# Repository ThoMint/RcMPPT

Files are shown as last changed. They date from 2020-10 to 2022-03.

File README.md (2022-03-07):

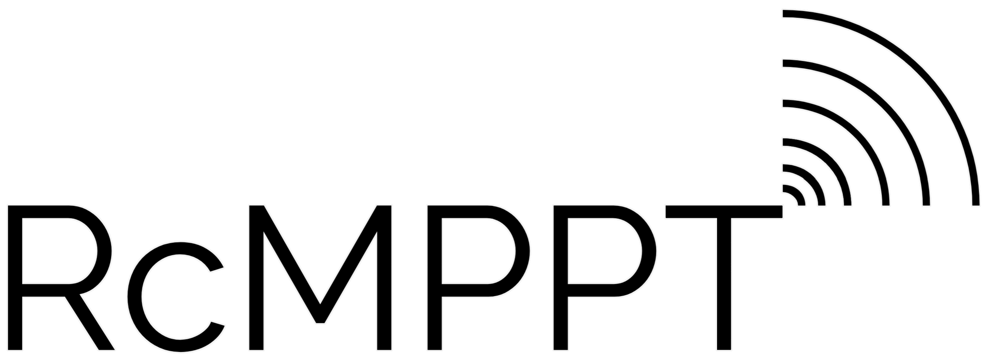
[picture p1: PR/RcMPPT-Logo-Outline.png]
RcMPPT

An MPPT Solar Charge Controller geared towards solar-powered RC model aircrafts and rovers\
\
Features:\
-SBUS/SPI/CAN/I2C/UART/USB Interface\
-Maximum Power Point Tracking\
-Extremely space/cost efficient\
-Ultra wide Vin/Vout Range 0-100V\
-High current capability 20A\

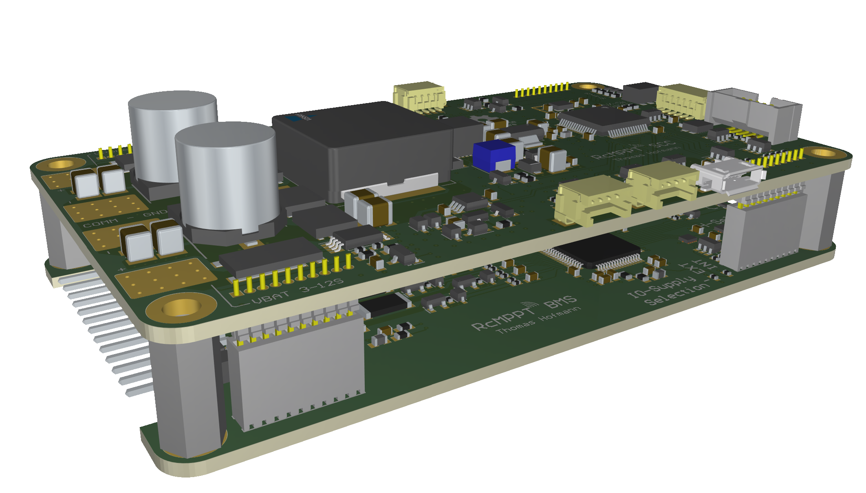
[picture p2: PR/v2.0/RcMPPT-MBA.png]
Side View of MBA Prototype


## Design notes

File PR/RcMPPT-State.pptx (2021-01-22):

## Rc-MPPT

Der Solar Charge Controller für Modellbau

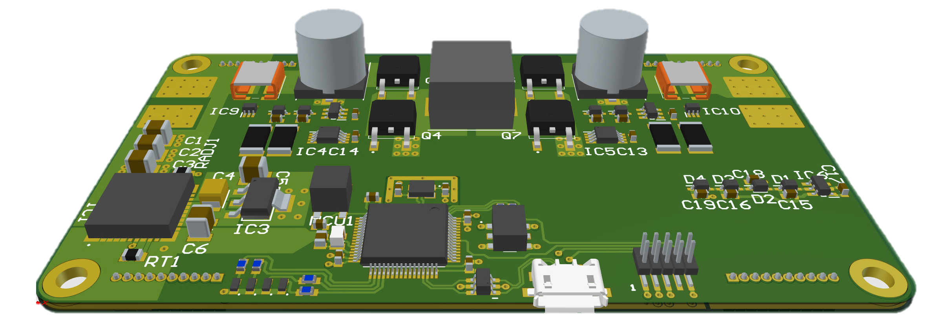
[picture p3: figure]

## Ziele: Project-Rover

- Solarbetriebenes Fahrzeug
- Testplattform für eigene Hardware
- Autonom (GPS-Wegpunktmissionen)

Hofmann Thomas 4BHELS

## Umfang: Project-Rover

- Solar-Rover als Testplattform für:
  - RcMPPT – Solarladeregler: modular | platz- und kosteneffizient | MPPT | Cell Balancing | 3-12S | Open Source
  - ModFOC – Motorregler: modular | platz-, kosten- und energieeffizient | BLDC / Stepper / DC | 3-12S | Open Source
  - Flexible Solarzellen: mögliche weitere Anwendungen evaluieren (Project-Airplane?)

## Motivation

- Technische Herausforderung
- Noch keine derartige Hardware für Modellbau auf dem Markt / Open Source

## Aufbau: RcMPPT

- MCU-getakteter 4-SW Buck Boost
  - Technische Herausforderung
  - Volle Kontrolle über Regelverhalten (CC, CV, Softstart, etc.) durch HRTIM
  - Kostenersparnis
- Logic Supply: 5V Rail Integrated Inductor Buck Schaltwandler
  - Kostenersparnis
  - Platzersparnis
- STM32G474RE
  - 32Bit MCU
  - Interfaces: S-BUS, I2C, SPI, CAN, USB, etc.

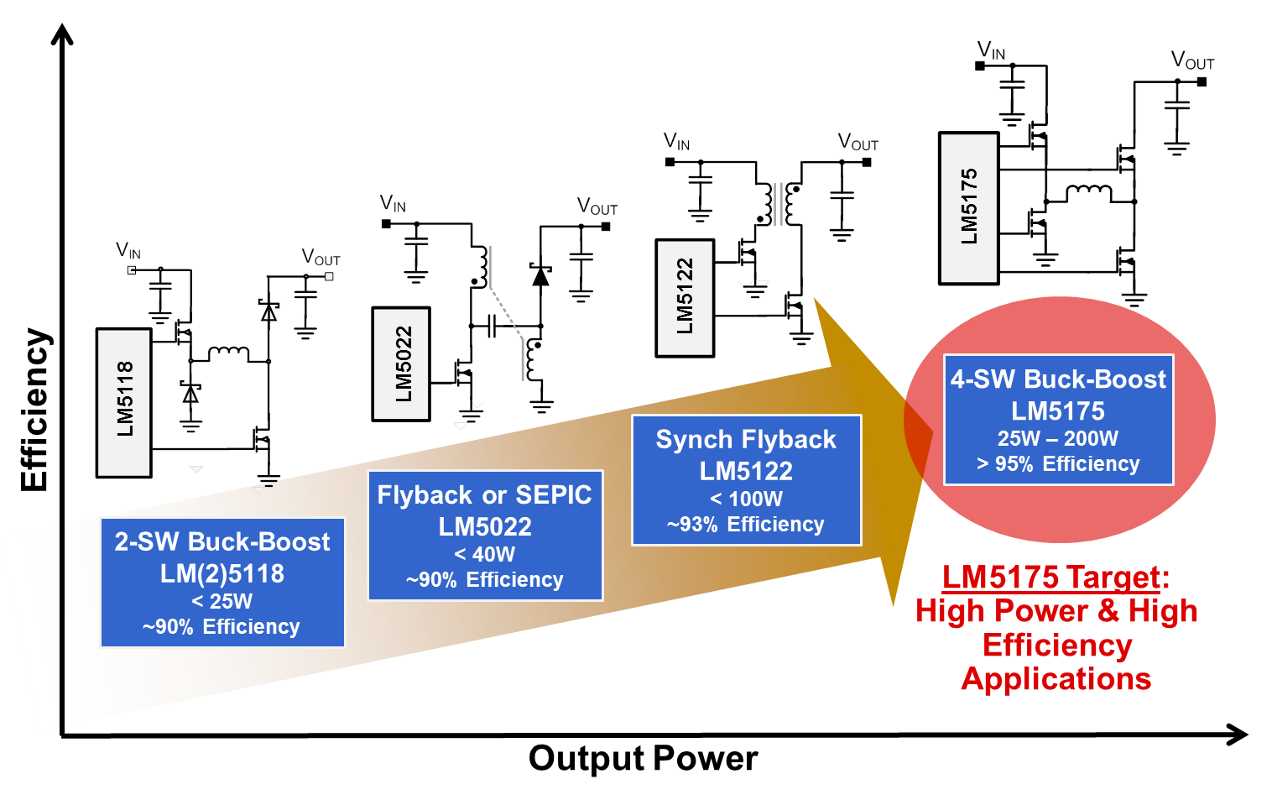
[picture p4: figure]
Four-switch buck-boost controller delivers high power and efficiency - Power management - Technical articles - TI E2E support forums

## Maximum Power Point Tracking

- Tracking durch Software
- Energiepuffer wird benötigt

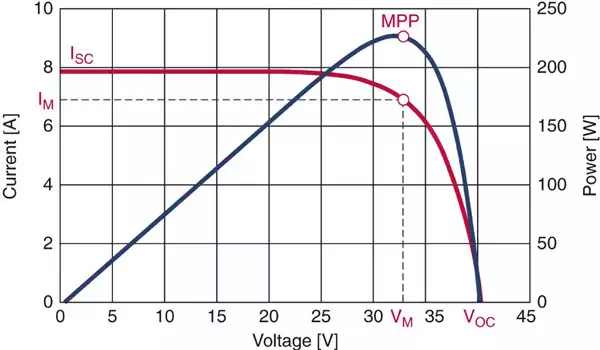
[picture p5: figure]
Maximum Power Point Tracking | BLUEsat UNSW

## Herausforderungen: RcMPPT

- Große Input / Output Voltage Range
  - 3-12S Output Voltage (6-60V)
  - 5V Logic Rail muss durch Buck Converter generiert werden (muss mit hohem Duty-Cycle arbeiten können)
- 4-Switch Buck Boost
  - High Side N-Kanal Mosfets -> Bootstrap Treiber
  - Für optimale Effizienz: Duty Cycle von 100% notwendig -> Floating Charge Pump
  - Hohe Schaltfrequenz

## Schematik: RcMPPT - MCU

- MCU
  - STM32G474RB
- Peripherie
  - Signal LEDS
  - Crystal Oszillator
  - USB
  - Decoupling / Analog Supply Filtering

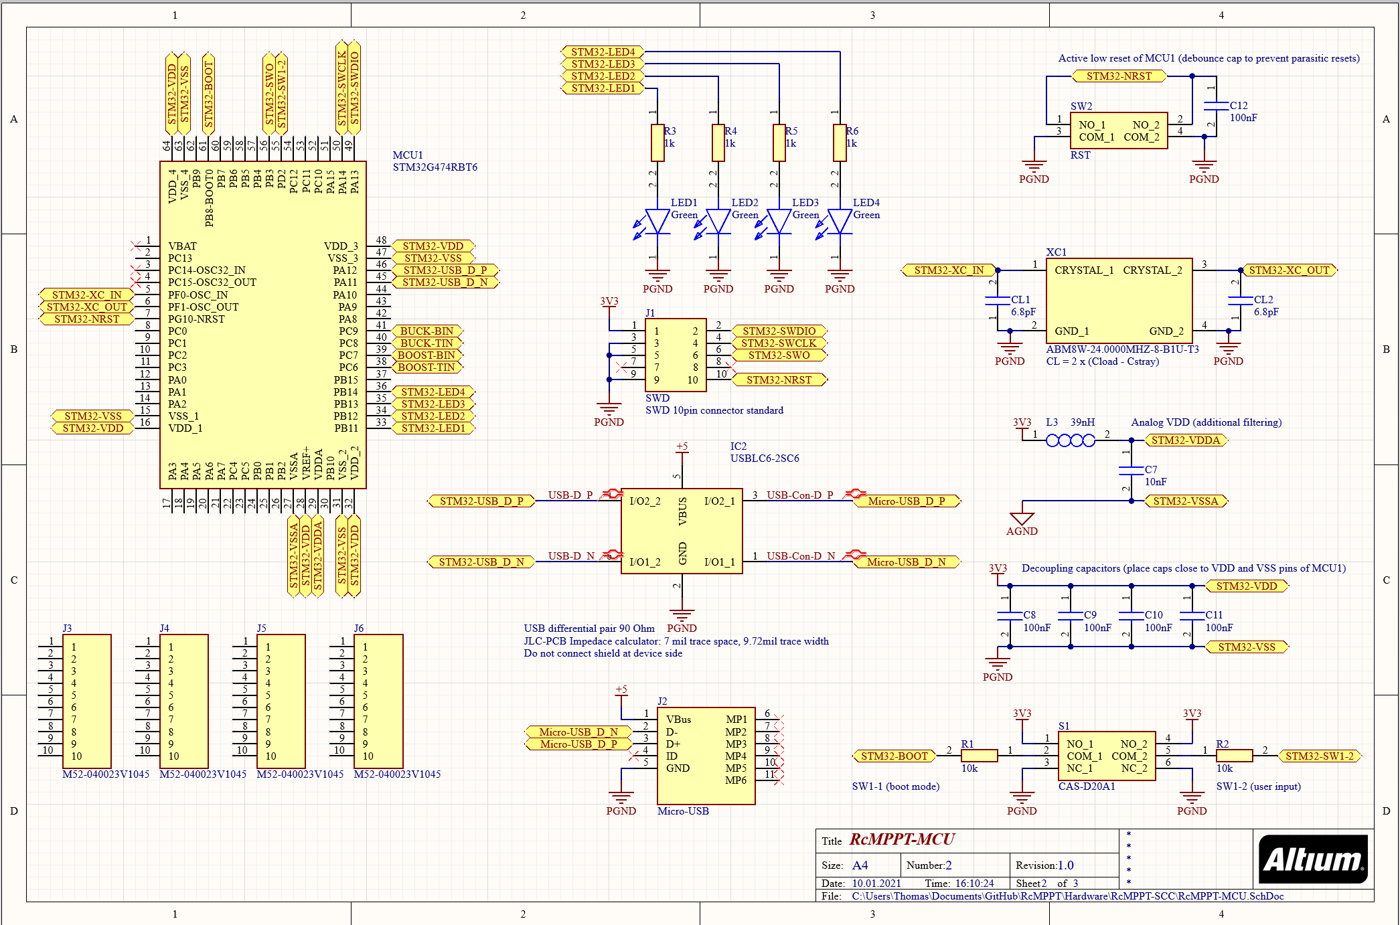
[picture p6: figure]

## SchematiK: RcMPPT – Power Module

- LMZ3600
  - Integrated Inductor
  - AGND, PGND
- 3V3 LDO
  - Low Ripple
  - Precision

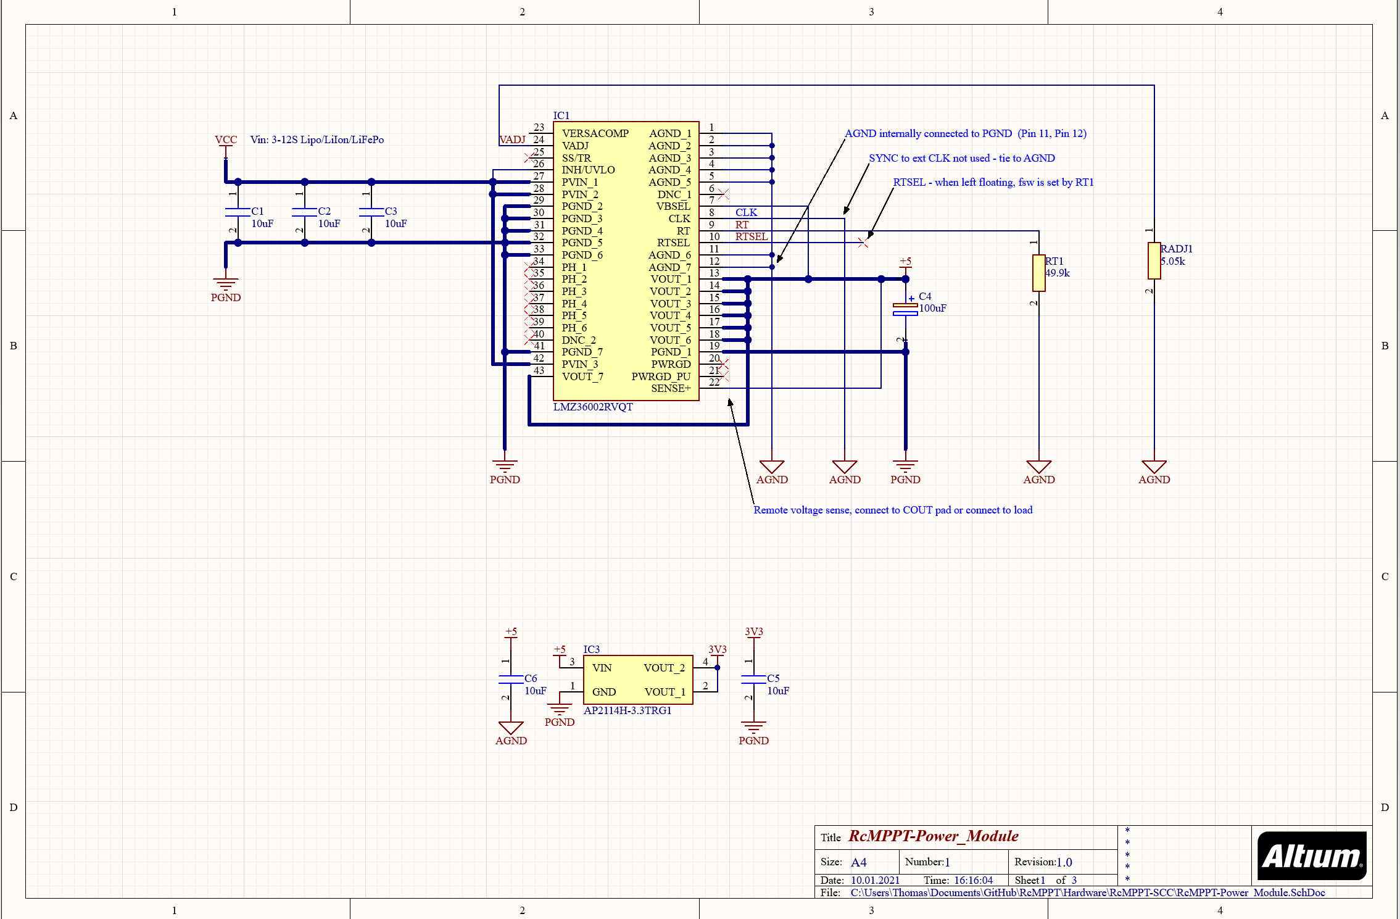
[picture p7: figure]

## Schematik: RcMPPT - DCDC

- 4Sw Buck Boost
  - Bootstrap Gate Driver
  - Floating Charge Pump (100% Duty Cycle)

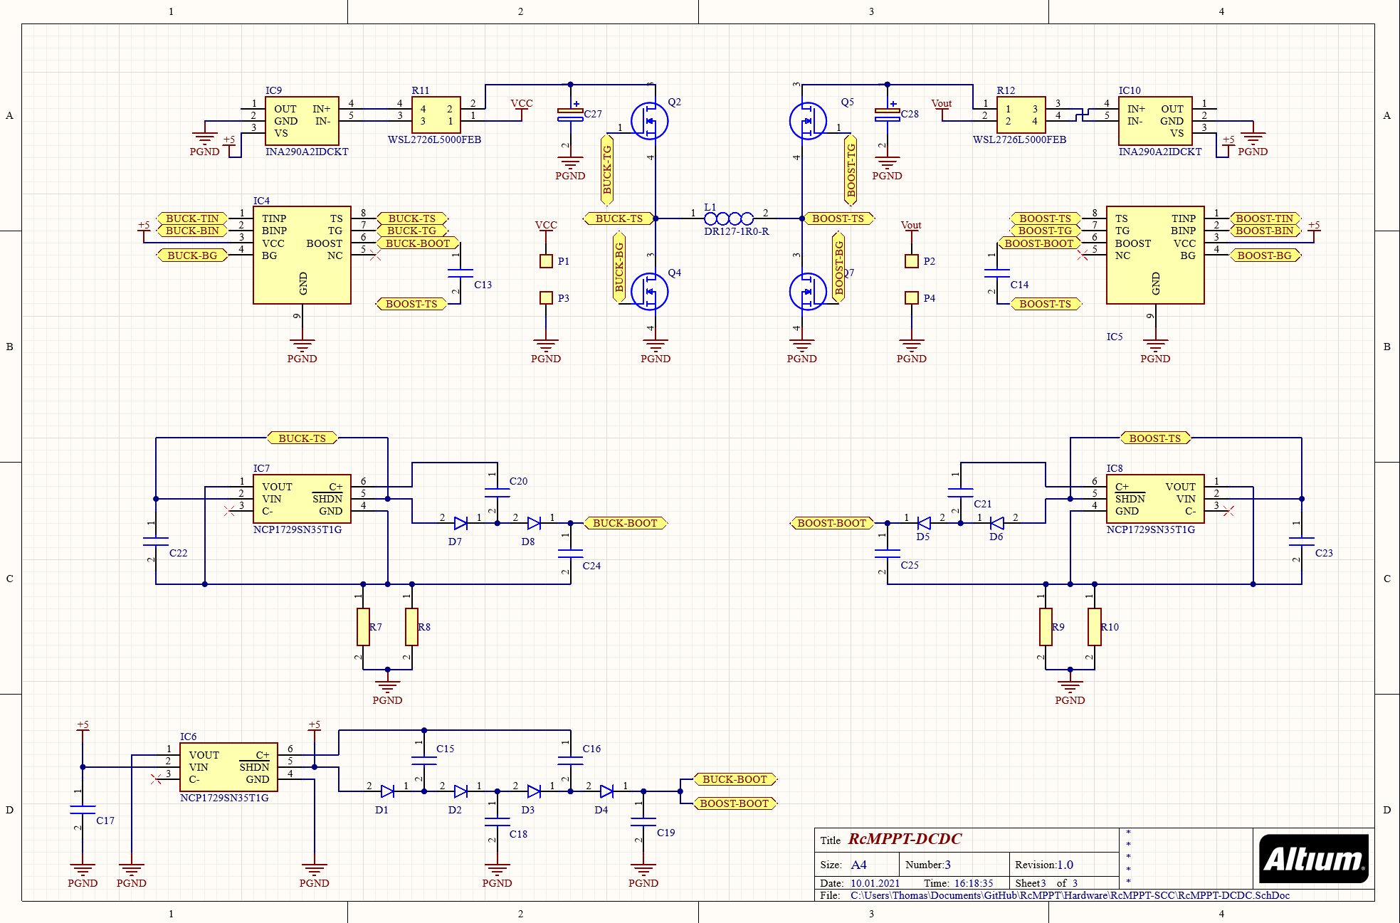
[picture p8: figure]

## Softwareentwicklung

- STM32CubeIDE
  - GUI Konfiguration von
    - Timer
    - Clock
    - Interfaces

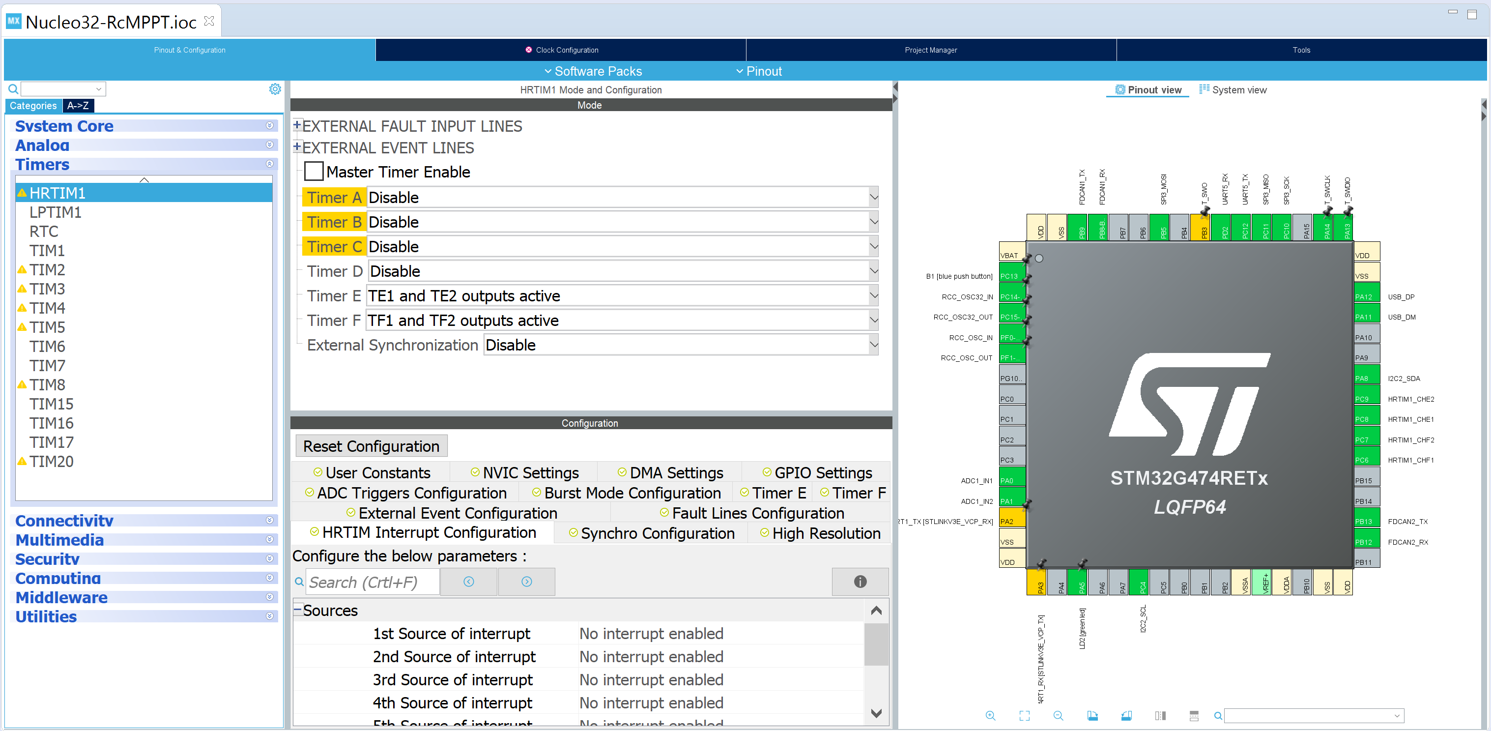
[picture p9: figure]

## Weitere Entwicklung

- PCB-Stackup
  - Solar Charge Controller
  - Battery Management System
- Software entwicklung
  - RcMPPT
  - ModFOC

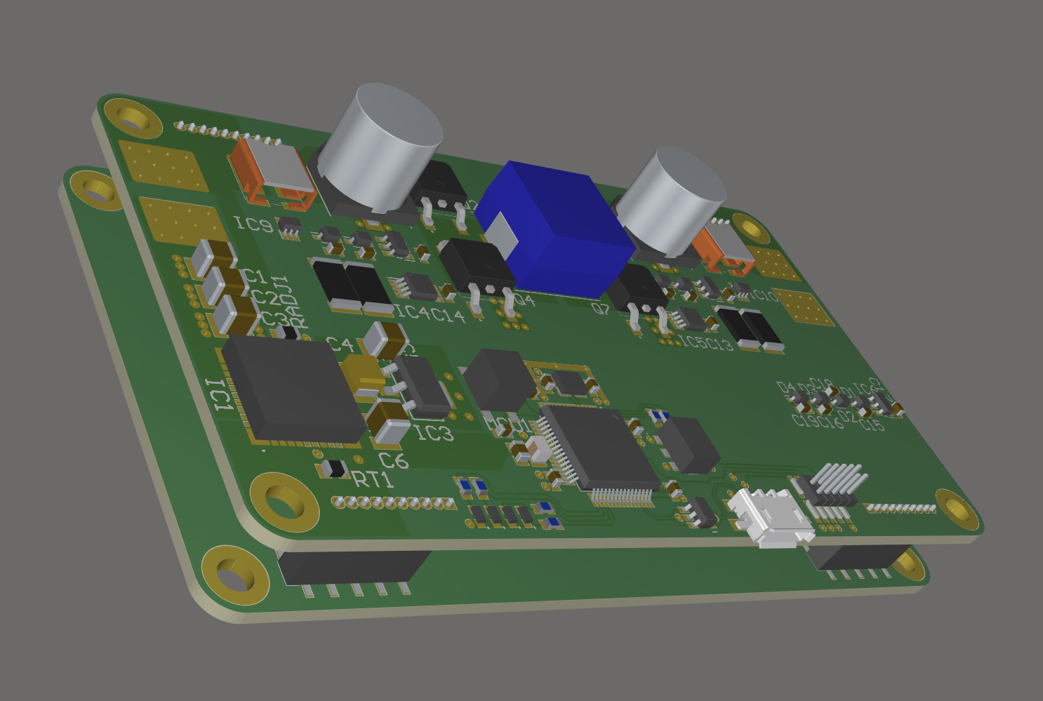
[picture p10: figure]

## Ende

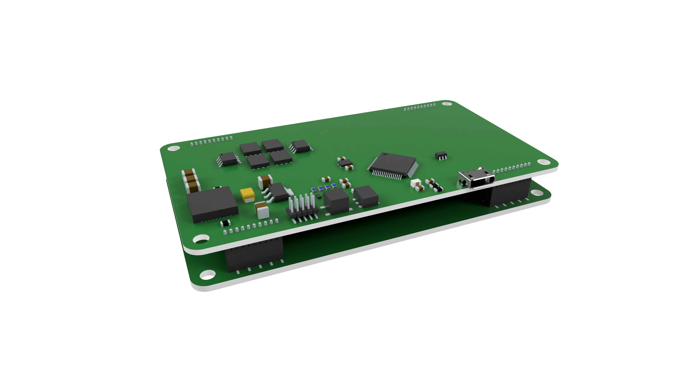
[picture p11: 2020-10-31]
Hardware/v2.0/RcMPPT/First_MBA_Prototype.png

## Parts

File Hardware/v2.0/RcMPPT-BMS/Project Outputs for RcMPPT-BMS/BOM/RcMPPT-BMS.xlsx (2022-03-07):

Comment | Description | Designator | Footprint | LibRef | Manufacturer_Part_Number | Manufacturer_Name | Mouser Part Number | Quantity
22-28-8133 | Connector | J1 | HDRRA13W66P0X254_1X13_3302X229X249P | 22-28-8133 | 22-28-8133 | Molex | 538-22-28-8133 | 1
BQ76PL536APAPT | Integrated Circuit | IC100, IC200 | QFP50P1200X1200X120-65N | BQ76PL536APAPT | BQ76PL536APAPT | Texas Instruments | 595-BQ76PL536APAPT | 2
2.2uF 10V | Capacitor | C108, C109, C110, C112, C114, C209, C210, C212, C214, C215 | CAPC1608X97N | C0603 | CL10A225KO8NNNC | Samsung Electro-Mechanics | 187-CL10A225KO8NNNC | 10
47nF 16V | Capacitor | C115, C116, C203, C204 | CAPC1608X97N | C0603 | CL10B473KO8NNNC | Samsung Electro-Mechanics | 187-CL10B473KO8NNNC | 4
100nF 6.3V | Capacitor | C400, C401 | CAPC1608X97N | C0603 | C0603C104K9RACTU | KEMET | 80-C0603C104K9R | 2
100nF 50V | Capacitor | C1, C100, C101, C102, C103, C104, C105, C106, C107, C111, C113, C200, C201, C202, C205, C206, C207, C208, C211, C213, C216, C300_U_RcMPPT-BMS-BFE-1-1, C300_U_RcMPPT-BMS-BFE-1-2, C300_U_RcMPPT-BMS-BFE-1-3, C300_U_RcMPPT-BMS-BFE-1-4, C300_U_RcMPPT-BMS-BFE-1-5, C300_U_RcMPPT-BMS-BFE-1-6, C300_U_RcMPPT-BMS-BFE-2-1, C300_U_RcMPPT-BMS-BFE-2-2, C300_U_RcMPPT-BMS-BFE-2-3, C300_U_RcMPPT-BMS-BFE-2-4, C300_U_RcMPPT-BMS-BFE-2-5, C300_U_RcMPPT-BMS-BFE-2-6 | CAPC1608X97N | C0603 | CL10B104JB8NNNC | Samsung Electro-Mechanics | 187-CL10B104JB8NNNC | 33
Green | LED | LED100, LED200 | CHIPLED_0603 | CHIPLED0603 | LT Q39G-Q1OO-25-1 | ams OSRAM | 720-LTQ39GQ1S22515 | 2
10k 1% NTC | Thermistor | RT100, RT101, RT200, RT201 | THRMC1608X90N | ERT-J1VG103FA | ERT-J1VG103FA | Panasonic | 667-ERT-J1VG103FA | 4
ESDSUPPRESSOR | TVS Diode Array | D400, D401 | SOT23-6 | ESDSUPPRESSOR | ESDALD05UD4X | WeEn Semiconductors | 771-ESDALD05UD4X | 2
60V 2A | MOSFET (N-Channel) | Q100, Q200, Q300_U_RcMPPT-BMS-BFE-1-1, Q300_U_RcMPPT-BMS-BFE-1-2, Q300_U_RcMPPT-BMS-BFE-1-3, Q300_U_RcMPPT-BMS-BFE-1-4, Q300_U_RcMPPT-BMS-BFE-1-5, Q300_U_RcMPPT-BMS-BFE-1-6, Q300_U_RcMPPT-BMS-BFE-2-1, Q300_U_RcMPPT-BMS-BFE-2-2, Q300_U_RcMPPT-BMS-BFE-2-3, Q300_U_RcMPPT-BMS-BFE-2-4, Q300_U_RcMPPT-BMS-BFE-2-5, Q300_U_RcMPPT-BMS-BFE-2-6 | SOT96P240X110-3N | NMOS | PMV37ENEAR | Nexperia | 771-PMV37ENEAR | 14
0R | Resistor | R114, R203, R408, R409 | RESC1005X40N | R0402 | ERJ-2GE0R00X | Panasonic | 667-ERJ-2GE0R00X | 4
1k | Resistor | R1, R2, R3, R4, R5, R6, R7, R8, R100, R101, R102, R103, R104, R105, R106, R107, R108, R109, R110, R111, R112, R205, R206, R207, R208, R209, R212, R215, R216, R218, R220, R221, R222, R223 | RESC1005X40N | R0402 | CR0402-FX-1001GLF | Bourns | 652-CR0402FX-1001GLF | 34
1M | Resistor | R301_U_RcMPPT-BMS-BFE-1-1, R301_U_RcMPPT-BMS-BFE-1-2, R301_U_RcMPPT-BMS-BFE-1-3, R301_U_RcMPPT-BMS-BFE-1-4, R301_U_RcMPPT-BMS-BFE-1-5, R301_U_RcMPPT-BMS-BFE-1-6, R301_U_RcMPPT-BMS-BFE-2-1, R301_U_RcMPPT-BMS-BFE-2-2, R301_U_RcMPPT-BMS-BFE-2-3, R301_U_RcMPPT-BMS-BFE-2-4, R301_U_RcMPPT-BMS-BFE-2-5, R301_U_RcMPPT-BMS-BFE-2-6 | RESC1005X40N | R0402 | RC0402FR-071ML | YAGEO | 603-RC0402FR-071ML | 12
2k2 | Resistor | R116, R200 | RESC1005X40N | R0402 | RC0402FR-072K2L | YAGEO | 603-RC0402FR-072K2L | 2
100k | Resistor | R113, R117, R201, R202 | RESC1005X40N | R0402 | ERJ-U02F1003X | Panasonic | 667-ERJ-U02F1003X | 4
100R | Resistor | R118, R119, R120, R204, R210, R211, R400, R401, R402, R403, R404, R405, R406, R407 | RESC1005X40N | R0402 | AC0402FR-13100RL | YAGEO | 603-AC0402FR-13100RL | 14
1.47k 1% | Resistor | R121, R122, R213, R214 | RESC1608X50N | R0603 | CR0603-FX-1471ELF | Bourns | 652-CR0603FX-1471ELF | 4
1.82k 1% | Resistor | R123, R124, R217, R219 | RESC1608X50N | R0603 | CR0603-FX-1821ELF | Bourns | 652-CR0603FX-1821ELF | 4
10R 1W | Resistor | R300_U_RcMPPT-BMS-BFE-1-1, R300_U_RcMPPT-BMS-BFE-1-2, R300_U_RcMPPT-BMS-BFE-1-3, R300_U_RcMPPT-BMS-BFE-1-4, R300_U_RcMPPT-BMS-BFE-1-5, R300_U_RcMPPT-BMS-BFE-1-6, R300_U_RcMPPT-BMS-BFE-2-1, R300_U_RcMPPT-BMS-BFE-2-2, R300_U_RcMPPT-BMS-BFE-2-3, R300_U_RcMPPT-BMS-BFE-2-4, R300_U_RcMPPT-BMS-BFE-2-5, R300_U_RcMPPT-BMS-BFE-2-6 | RESC6331X75N | R2512 | CR2512-JW-100ELF | Bourns | 652-CR2512-JW-100ELF | 12
SMS-110-01-G-S | 10 Position Receptacle Connector 0.050" (1.27mm) Through Hole Gold | J400, J401, J402, J403 | SAMTEC_SMS-110-X-X-S | SMS-110-X-X-S | SMS-110-01-G-S | Samtec | 200-SMS11001GS | 4
TXU0304RUTR | Integrated Circuit | IC400, IC401 | UQFN-12 | TXU0304RUTR | TXU0304RUTR | Texas Instruments | 595-TXU0304RUTR | 2
5.1V 200mW | ZENER Diode | D301_U_RcMPPT-BMS-BFE-1-1, D301_U_RcMPPT-BMS-BFE-1-2, D301_U_RcMPPT-BMS-BFE-1-3, D301_U_RcMPPT-BMS-BFE-1-4, D301_U_RcMPPT-BMS-BFE-1-5, D301_U_RcMPPT-BMS-BFE-1-6, D301_U_RcMPPT-BMS-BFE-2-1, D301_U_RcMPPT-BMS-BFE-2-2, D301_U_RcMPPT-BMS-BFE-2-3, D301_U_RcMPPT-BMS-BFE-2-4, D301_U_RcMPPT-BMS-BFE-2-5, D301_U_RcMPPT-BMS-BFE-2-6 | SOD-323 | ZENER-DIODE | MMXZ5231B-TP | Micro Commercial Components (MCC) | 833-MMXZ5231B-TP | 12
5.6V 400mW | ZENER Diode | D300_U_RcMPPT-BMS-BFE-1-1, D300_U_RcMPPT-BMS-BFE-1-2, D300_U_RcMPPT-BMS-BFE-1-3, D300_U_RcMPPT-BMS-BFE-1-4, D300_U_RcMPPT-BMS-BFE-1-5, D300_U_RcMPPT-BMS-BFE-1-6, D300_U_RcMPPT-BMS-BFE-2-1, D300_U_RcMPPT-BMS-BFE-2-2, D300_U_RcMPPT-BMS-BFE-2-3, D300_U_RcMPPT-BMS-BFE-2-4, D300_U_RcMPPT-BMS-BFE-2-5, D300_U_RcMPPT-BMS-BFE-2-6 | SOD-123FL | ZENER-DIODE | NZH5V6B,115 | Nexperia | 771-NZH5V6B-115 | 12

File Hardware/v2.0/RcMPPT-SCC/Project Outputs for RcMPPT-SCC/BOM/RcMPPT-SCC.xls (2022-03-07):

Designator | Comment | DesignItemId | Footprint | Manufacturer_Part_Number | Manufacturer_Name | Mouser Part Number | Quantity
R106, R107, R410, R411, R504, R505, R506, R507 | 1k | R0603 | RESC1608X50N | CR0603-FX-1001ELF (https://www.mouser.at/ProductDetail/Bourns/CR0603-FX-1001ELF) | Bourns (https://www.mouser.at/manufacturer/bourns/) | 652-CR0603FX-1001ELF | 8
R414, R601 | 1M | R0603 | RESC1608X50N | RC0603FR-131ML (https://www.mouser.at/ProductDetail/YAGEO/RC0603FR-131ML?qs=sGAEpiMZZMvdGkrng054t8AJgcdMkx7xUtJ5VXpD6XA%3D) | YAGEO (https://www.mouser.at/manufacturer/yageo/) | 603-RC0603FR-131ML | 2
R104, R105, R310, R311 | 2k | R0603 | RESC1608X50N | RK73B1JTTD202J (https://www.mouser.at/ProductDetail/KOA-Speer/RK73B1JTTD202J) | KOA Speer (https://www.mouser.at/manufacturer/koa-speer/) | 660-RK73B1JTTD202J | 4
R304, R305 | 2k | R0402 | RESC1005X40N | ERJ-2RKF2001X (https://www.mouser.at/ProductDetail/Panasonic/ERJ-2RKF2001X?qs=sGAEpiMZZMvdGkrng054t8ugkoYZivkgNOCNyJBEp2c%3D) | Panasonic (https://www.mouser.at/manufacturer/panasonicec/) | 667-ERJ-2RKF2001X | 2
IC600 | 3V3 >800mA | LDO-SOT223 | SOT230P700X180-4N | NCP1117ST33T3G (https://www.mouser.at/ProductDetail/onsemi/NCP1117ST33T3G) | onsemi (https://www.mouser.at/manufacturer/onsemi/) | 863-NCP1117ST33T3G | 1
C306, C307, C316, C317 | 3.3uF 16V | C0603 | CAPC1608X97N | C1608X5R1C335K080AC (https://www.mouser.at/ProductDetail/TDK/C1608X5R1C335K080AC?qs=U4gclJHtfSguGhrrYC%2Fi2g%3D%3D) | TDK (https://www.mouser.at/manufacturer/tdk/) | 810-C1608X5R1C335KAC | 4
R308, R309 | 4k3 | R0603 | RESC1608X50N | CR0603-JW-432ELF (https://www.mouser.at/ProductDetail/Bourns/CR0603-JW-432ELF) | Bourns (https://www.mouser.at/manufacturer/bourns/) | 652-CR0603JW-432ELF | 2
CL100, CL101 | 4nF 6.3V | C0603 | CAPC1608X97N | CL10C040CB8NNNC (https://www.mouser.at/ProductDetail/Samsung-Electro-Mechanics/CL10C040CB8NNNC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) | Samsung (https://www.mouser.at/manufacturer/samsung-electro-mechanics/) | 187-CL10C040CB8NNNC | 2
C201, C202 | 4.7uF 100V | C1210 | CAPC3225X270N | CL32B475KCVZNWE (https://www.mouser.at/ProductDetail/Samsung-Electro-Mechanics/CL32B475KCVZNWE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) | Samsung | 187-CL32B475KCVZNWE | 2
R300, R301 | 5mR 4W | FC4L90R005FER | FC4L90R005FER | FC4L90R005FER | Ohmite | 588-FC4L90R005FER | 2
R100, R102, R103, R400, R403, R404, R409 | 10k | R0603 | RESC1608X50N | RC0603JR-0710KL (https://www.mouser.at/ProductDetail/YAGEO/RC0603JR-0710KL?qs=sGAEpiMZZMvdGkrng054txdMlaQGj9fi5a0YMwYlB2s%3D) | YAGEO (https://www.mouser.at/manufacturer/yageo/) | 603-RC0603JR-0710KL | 7
C105, C112, C401 | 10nF 6.3V | C0603 | CAPC1608X97N | C0603C103K9RACTU (https://www.mouser.at/ProductDetail/KEMET/C0603C103K9RACTU?qs=r%2FVmNO8Tjq6U7vsVOlbauA%3D%3D) | KEMET (https://www.mouser.at/manufacturer/kemet-electronics/) | 80-C0603C103K9R | 3
C600, C601 | 10uF 6.3V X7R | C1206 | CAPC3216X180N | CL31B106KQHNFNE (https://www.mouser.at/ProductDetail/Samsung-Electro-Mechanics/CL31B106KQHNFNE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) | Samsung | 187-CL31B106KQHNFNE | 2
C308, C309 | 10uF 16V | C0805 | CAPC2012X88N | CL21A106KOQNNNG (https://www.mouser.at/ProductDetail/Samsung-Electro-Mechanics/CL21A106KOQNNNG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) | Samsung | 187-CL21A106KOQNNNG | 2
C603, C604 | 10uF 25V X7R | C1210 | CAPC3225X270N | TMK325B7106KN-TR (https://www.mouser.at/ProductDetail/Taiyo-Yuden/TMK325B7106KN-TR?qs=PzICbMaShUf6mn8bIhLveg%3D%3D) | Taiyo Yuden (https://www.mouser.at/manufacturer/taiyo-yuden/) | 963-TMK325B7106KN-TR | 2
C300, C301, C302, C303, C312, C313, C314, C315 | 10uF 100V | C1210 | CAPC3225X270N | GRM32EC72A106KE05L | Murata Electronics | 81-GRM32EC72A106KE05 | 8
L600 | 12uH | 78438357100 | INDPM4141X310N | 78438357100 | Wurth Elektronik | 710-78438357100 | 1
R602 | 13.3k | R0603 | RESC1608X50N | ERJ-3EKF1332V (https://www.mouser.at/ProductDetail/Panasonic/ERJ-3EKF1332V?qs=sGAEpiMZZMvdGkrng054t8ugkoYZivkgWToiCCR9eDI%3D) | Panasonic (https://www.mouser.at/manufacturer/panasonicec/) | 667-ERJ-3EKF1332V | 1
Y100 | 16Mhz 8pF | ABM8W-16.0000MHZ-8-B1U-T3 | ABM8W160000MHZ8B1UT3 | ABM8W-16.0000MHZ-8-B1U-T3 | ABRACON | 815-8W16-8B1UT | 1
C200 | 16pF 50V | C0603 | CAPC1608X97N | CC0603JRNPO9BN150 (https://www.mouser.at/ProductDetail/YAGEO/CC0603JRNPO9BN150?qs=lZqiD2QyRYKNhZfO2ANLDw%3D%3D) | YAGEO (https://www.mouser.at/manufacturer/yageo/) | 603-CC603JRNPO9BN150 | 1
R302, R303 | 18k | R0402 | RESC1005X40N | AA0402FR-0718KL (https://www.mouser.at/ProductDetail/YAGEO/AA0402FR-0718KL) | YAGEO (https://www.mouser.at/manufacturer/yageo/) | 603-AA0402FR-0718KL | 2
D600 | 20V 1A/45A | SCHOTTKY-DIODE | SOD-123FL | RSX101MM-30TFTR | ROHM Semiconductor | 755-RSX101MM-30TFTR | 1
R101 | 22R | R0402 | RESC1005X40N | CR0402-FX-22R0GLF | Bourns | 652-CR0402FX-22R0GLF | 1
C203, C204 | 22uF 6.3V | C1210 | CAPC3225X270N | JMK325BJ226MM-T | Taiyo Yuden | 963-JMK325BJ226MM-T | 2
Rfb201 | 24.9k 1% | R0603 | RESC1608X50N | RC0603FR-0724K9L (https://www.mouser.at/ProductDetail/YAGEO/RC0603FR-0724K9L) | YAGEO | 603-RC0603FR-0724K9L | 1
D306, D307, D400 | 30V 1A | SCHOTTKY-DIODE | SOD-323 | CUS10S30,H3F | Toshiba | 757-CUS10S30H3F | 3
C310, C311 | 47uF 100VDC 10mm | ELKO | CAPAE1030X1050N | MAL214699904E3 | Vishay / BC Components | 594-MAL214699904E3 | 2
R306, R307 | 82k | R0603 | RESC1608X50N | CRCW060382K0FKEAC | Vishay / Dale | 71-CRCW060382K0FKEAC | 2
Rfb200 | 100k 1% | R0603 | RESC1608X50N | CRCW0603100KFKEC | Vishay / Dale | 71-CRCW0603100KFKEC | 1
C100, C106, C107, C108, C109, C110, C111, C304, C305, C402, C500 | 100nF 6.3V | C0603 | CAPC1608X97N | C0603C104K9RACTU | KEMET | 80-C0603C104K9R | 11
C101, C102, C103, C104 | 100nF 6.3V | C0402 | CAPC1005X55N | 04026D104KAT2A | Kyocera AVX | 581-04026D104KAT2A | 4
R401, R402, R405, R406, R407, R408, R412, R413, R500, R501, R502, R503, R700, R701, R702, R703, R704, R705, R706, R707 | 100R | R0402 | RESC1005X40N | RC0402JR-13100RL | YAGEO | 603-RC0402JR-13100RL | 20
D302, D303, D304, D305, D308, D309 | 100V 1A | SCHOTTKY-DIODE | SOD-323 | BAS3010A03WE6327XT | Infineon Technologies | 726-BAS3010A03WE632 | 6
D200, D201 | 100V 2A | SCHOTTKY-DIODE | SOD-123FL | NRVBS310FA | onsemi (https://www.mouser.at/manufacturer/onsemi/) | 863-NRVBS310FA | 2
Q304, Q305, Q306, Q307 | 100V 2A | NMOS | SI2305TP | SI2324DS-T1-GE3 | Vishay Semiconductors | 78-SI2324DS-T1-GE3 | 4
R600 | 118k | R0603 | RESC1608X50N | CR0603-FX-1183ELF | Bourns | 652-CR0603FX-1183ELF | 1
FB100 | 220R @ 100MHz | FB0603 | FB0603 | MPZ1608S221ATA00 | TDK | 810-MPZ1608S221ATA00 | 1
C602 | 270pF 50V NP0 | C0603 | CAPC1608X97N | C0603C271J5GACTU | KEMET | 80-C0603C271J5G | 1
J401 | 1981584-1 | 1981584-1 | 19815841 | 1981584-1 | TE Connectivity | 571-1981584-1 | 1
S100 | 434153017835 | SW-SPST | 434153017835 | 710-434153017835 | Wurth Elektronik | 434153017835 | 1
D300, D301 | BAT54SQ-7-F | BAT54SQ-7-F | SOT96P240X110-3N | BAT54SQ-7-F | Diodes Inc. | 621-BAT54SQ-7-F | 2
Q100, Q101, Q400, Q401 | BC847A | BC847A,235 | SOT95P230X110-3N | BC847A,235 | Nexperia | 771-BC847A235 | 4
S101 | CAS-D20A1 | CAS-D20A1 | CASD20A1 | CAS-D20A1 | Copal Electronics | 229-CAS-D20A1 | 1
J403, J404, J405 | DF13A-4P-1.25H_21_ | DF13A-4P-1.25H_21_ | DF13A4P125H21 | DF13A-4P-1.25H(21) | Hirose | 798-DF13A4P125H21 | 3
J402 | DF13A-6P-1.25H_21_ | DF13A-6P-1.25H_21_ | DF13A6P125H21 | DF13A-6P-1.25H(21) | Hirose | 798-DF13A6P125H21 | 1
D401, D402, D403, D404, D500, D700, D701 | ESDSUPPRESSOR | ESDSUPPRESSOR | SOT23-6 | ESDALD05UD4X | WeEn Semiconductors | 771-ESDALD05UD4X | 7
LED500, LED501, LED502, LED503 | Green | CHIPLED0603 | CHIPLED_0603 | LT Q39G-Q1OO-25-1 | ams OSRAM | 720-LTQ39GQ1S22515 | 4
L300 | IHLP6767GZER2R2M01 | IHLP6767GZER2R2M01 | FP-IHLP-6767GZ-FP_3_825x1-MFG | IHLP6767GZER2R2M01 | Vishay / Dale | 70-IHLP6767GZER2R2M0 | 1
IC300, IC301 | INA240A4PWR | INA240A4PWR | SOP65P640X120-8N | INA240A4PWR | Texas Instruments | 595-INA240A4PWR | 2
S600 | LMR62014XMF_NOPB | LMR62014XMF_NOPB | SOT95P280X145-5N | LMR62014XMF/NOPB | Texas Instruments | 926-LMR62014XMF/NOPB | 1
IC302, IC303 | LTC4444EMS8E-5#PBF | LTC4444EMS8E-5#PBF | SOP65P490X110-9N | LTC4444EMS8E-5#PBF | Linear Technology | 584-C4444EMS8E-5PBF | 2
Q300, Q301, Q302, Q303 | SIR680ADP-T1-RE3 | SIR680ADP-T1-RE3 | SI7141DPT1GE3 | SIR680ADP-T1-RE3 | Vishay | 78-SIR680ADP-T1-RE3 | 4
IC100 | STM32G474RBT6 | STM32G474RBT6 | QFP50P1200X1200X160-64N | STM32G474RBT6 | STMicroelectronics | 511-STM32G474RBT6 | 1
J500 | SWD Connector | M50-3600542R | HUSSP10W40P127_2X5_635X340X420P | M50-3600542R | Harwin | 855-M50-3600542R | 1
J700, J701, J702, J703 | TMS-110-01-G-S | TMS-110-01-G-S | SAMTEC_TMS-110-01-G-S | TMS-110-01-G-S | Samtec | 200-TMS11001GS | 4
IC200 | TPSM5601R5HSRDAR | TPSM5601R5HSRDAR | TPSM5601R5HSRDAR | TPSM5601R5HSRDAR | Texas Instruments | 595-TPSM5601R5HSRDAR | 1
IC400 | USBLC6-2SC6 | USBLC6-2SC6 | SOT95P280X145-6N | USBLC6-2SC6 | STMicroelectronics | 511-USBLC6-2SC6 | 1

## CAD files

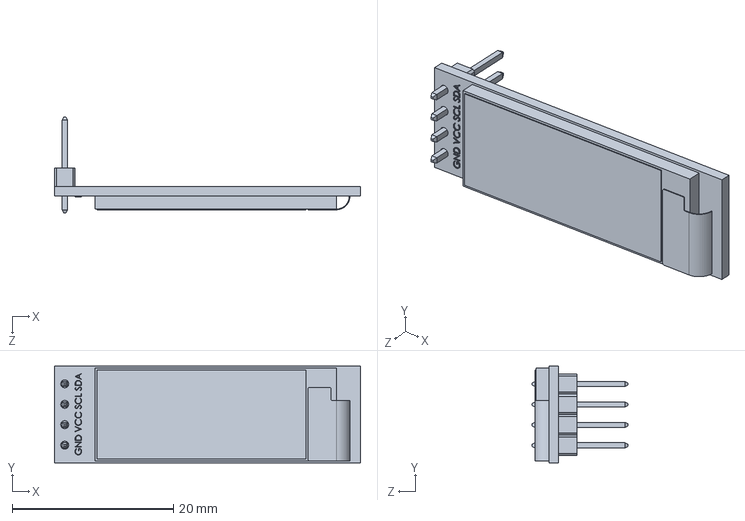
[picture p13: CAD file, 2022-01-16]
Hardware/v2.0/RcMPPTLib/128x32-OLED.STEP
38.0 x 12.0 x 11.9 mm

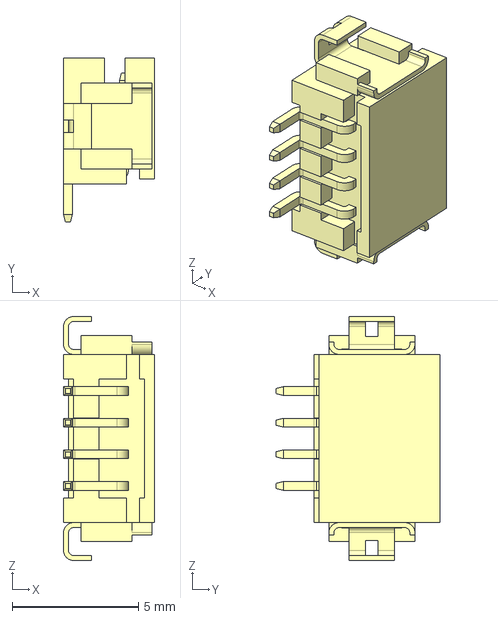
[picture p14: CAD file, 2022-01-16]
Hardware/v2.0/RcMPPTLib/DF13A-4P-1.25H.stp
3.60 x 6.50 x 9.65 mm

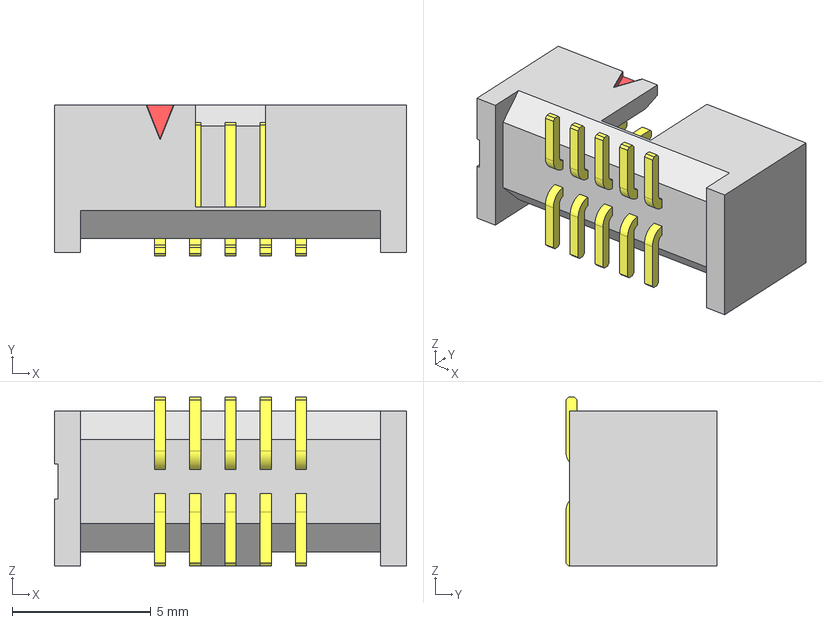
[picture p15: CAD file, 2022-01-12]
Hardware/v2.0/RcMPPTLib/SHF-105-01-S-D-SM.stp
12.7 x 5.46 x 6.10 mm
_SHF-105-01-D_header
_SHF-First_Position_Indicator
_T-1S71-02-05-D-SM

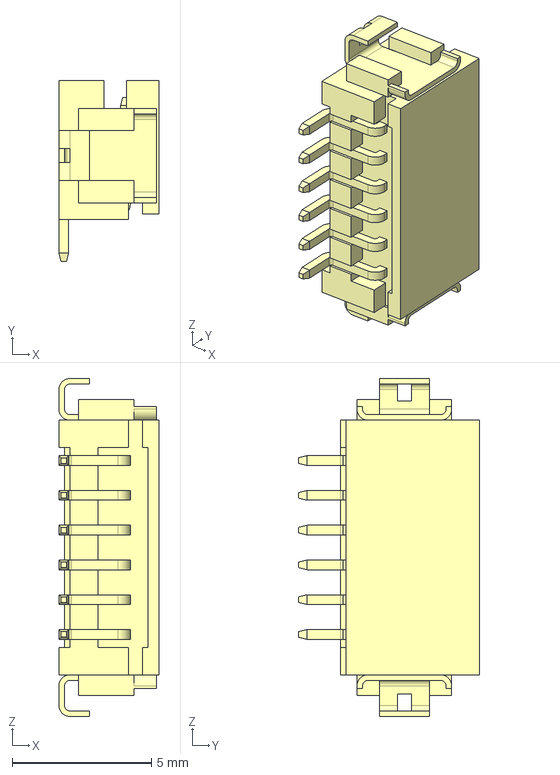
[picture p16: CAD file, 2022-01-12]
Hardware/v2.0/RcMPPTLib/DF13A-6P-1.25H.stp
3.60 x 6.50 x 12.1 mm

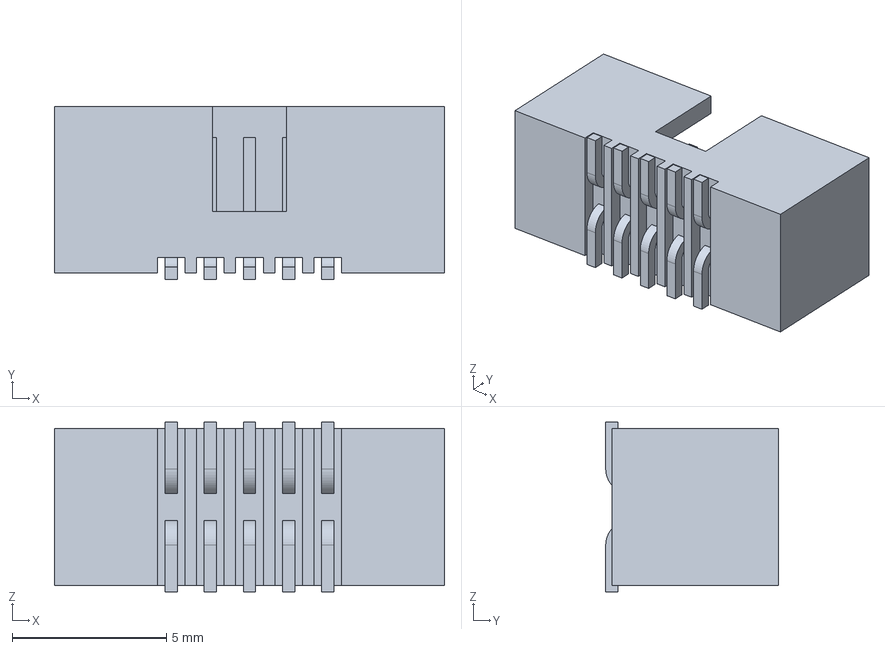
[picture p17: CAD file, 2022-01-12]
Hardware/v2.0/RcMPPTLib/20021521-00010XXLFc.stp
12.7 x 5.60 x 5.50 mm

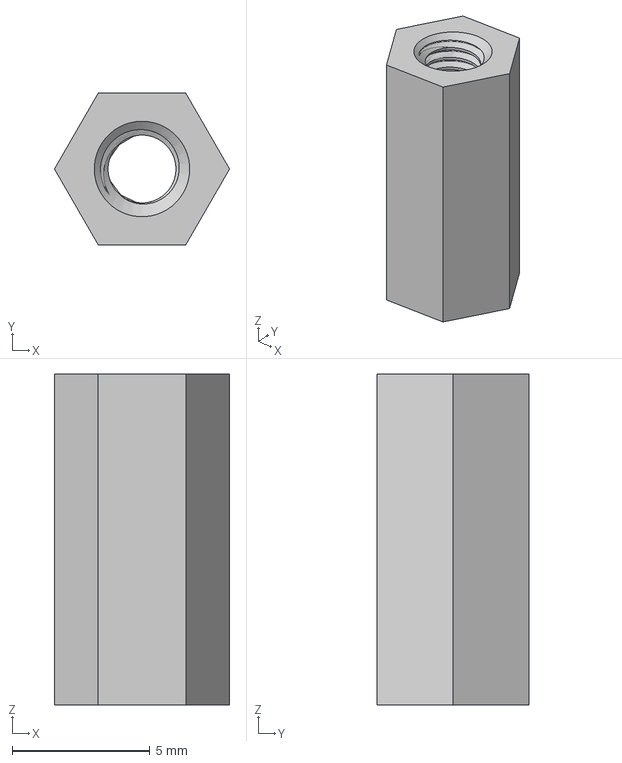
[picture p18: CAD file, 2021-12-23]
Hardware/v2.0/RcMPPTLib/hex spacer standoff nut_M3 L12.stp
6.35 x 5.50 x 12.0 mm

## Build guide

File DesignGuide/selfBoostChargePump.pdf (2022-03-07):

300 | IEEE TRANSACTIONS ON POWER ELECTRONICS, VOL. 20, NO. 2, MARCH 2005

# A Self-Boost Charge Pump Topology for a Gate Drive High-Side Power Supply

Shihong Park, Student Member, IEEE, and Thomas M. Jahns, Fellow, IEEE

Abstract—A self-boost charge pump topology is presented for a floating high-side gate drive power supply that features high voltage and current capabilities for use in integrated power electronic modules (IPEMs). The transformerless topology uses a small capacitor to transfer energy to the high-side switch from a single power supply referred to the negative rail. Unlike conventional bootstrap power supplies, no switching of the main phase-leg switches is required to provide power continuously to the high-side gate drive, even if the high-side switch is permanently on. Additional advantages include low parts-count and simple control requirements. A piecewise linear model of the self-boost charge pump is derived and the circuit’s operating characteristics are analyzed. Simulation and experimental results are provided to verify the desired operation of the new charge pump circuit. Guidelines are provided to assist with circuit component selection in new applications.

Index Terms—Bootstrap power supply, floating, high-side gate drive, MOS-gated power semiconductors, power module, transformerless.

I. INTRODUCTION
A. Background
B OOTSTRAP circuits are widely used in bridge inverters to provide the floating power supply for high-side switch gate drives [1]. They are often preferred over high-frequency transformer circuits due to their simplicity and basic compatibility with integrated circuit implementation, making them well suited for achieving low cost and high reliability.
However, the bootstrap technique imposes significant limitations due to its periodic charging time requirements that can interfere with the desired gate drive operation under some important operating conditions [1]. In particular, the high-side gate drive can become starved of energy if the inverter switching algorithm calls for either switch to be on for long intervals. Under such circumstances, the main phase-leg switch may be forced to perform a brief switching cycle in order to refresh the depleted capacitor charge for the high-side gate drive.
One approach that has been proposed to overcome these problems uses an auxiliary charge pump [2]–[4]. This technique can

Manuscript received March 31, 2003; revised August 18, 2004. This work was supported by the ERC Program of the U.S. National Science Foundation under Award EEC-9731677 and by the Wisconsin Electric Machines and Power Electronics Consortium (WEMPEC). Recommended by Associate Editor F. Blaabjerg.
S. Park is with the School of Electrical, Electronics, and Computer Engineering, Dankook University, Seoul 140-714, Korea (e-mail: shihong@ dankook.ac.kr).
T. M. Jahns is with the University of Wisconsin-Madison, Madison, WI 53706 USA (e-mail: t.jahns@ieee.org).
Digital Object Identifier 10.1109/TPEL.2004.843013

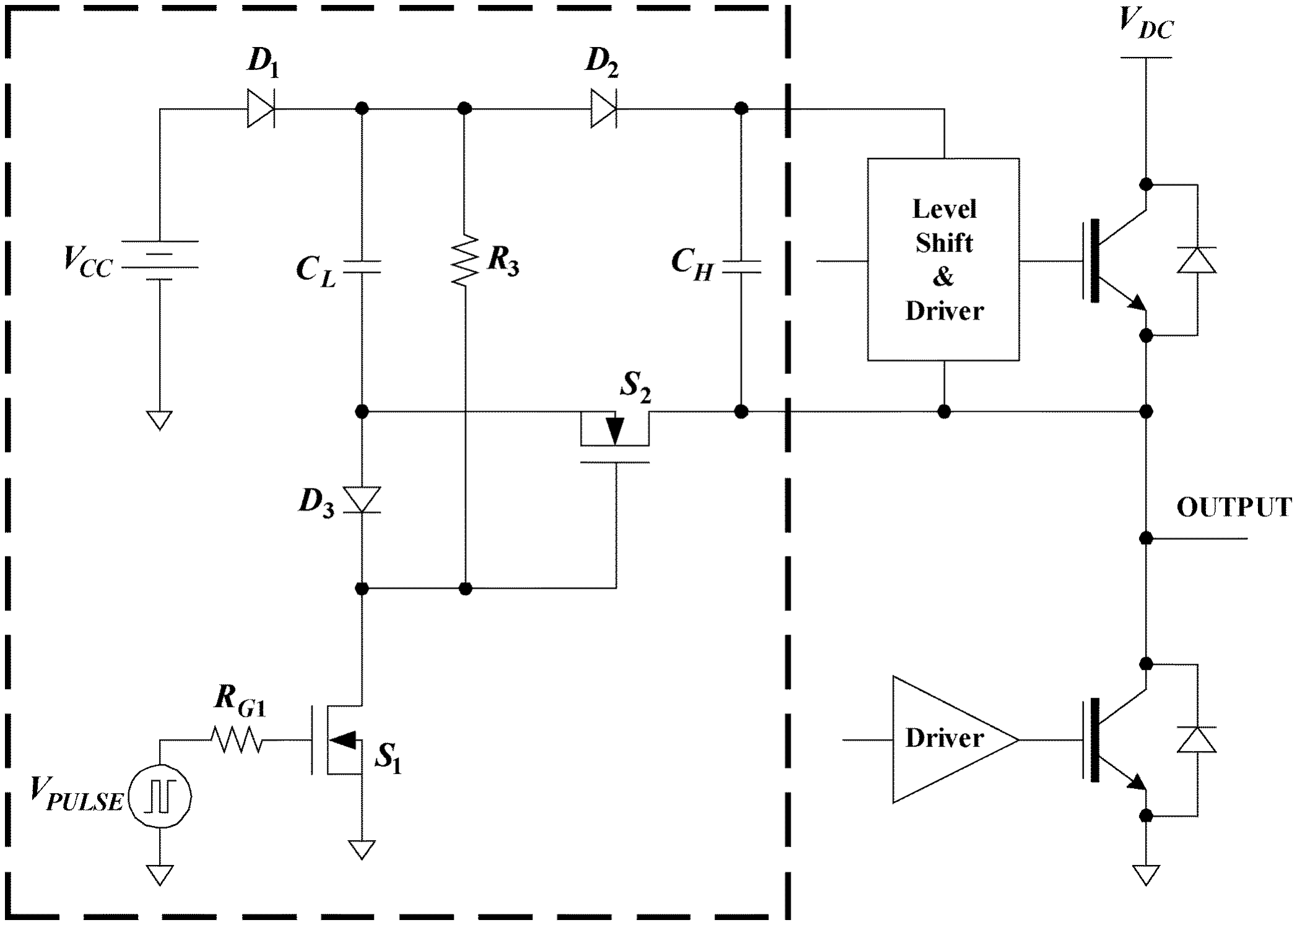
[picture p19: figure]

Fig. 1. Self-boost charge pump circuit configuration for an inverter phase leg high-side power supply.

provide the needed power for a high-side gate drive without interfering with the desired phase-leg switching sequence. However, it is not widely used due to its higher complexity and its requirements for high-voltage level shifting to supply control signals to the auxiliary switches.
Another technique has been described in the literature [5],
[6] that applies charge pump techniques to deliver power to a floating high-side power supply. It has a simple topology and overcomes the limitation of conventional bootstrap high-side power supplies by transferring charge even when the upper switch is permanently on. However, this technique suffers in high current applications from high power losses in the charge pump oscillator and high voltage ripple due to large voltage surges caused by switching of the main phase-leg switches. These disadvantages limit this technique to gate drive applications with low current supply requirements.
A new charge pump topology is presented in this paper for floating high-side gate drive power supplies that avoid the problems of existing techniques while retaining the advantages of simplicity and compatibility with integrated circuit implementation. This topology, shown in Fig. 1 with a standard inverter phase leg, uses a modified charge-pump circuit to deliver power from the low side to the high side.
B. Operating Principles

The operation of this new charge-pump circuit can be divided into the following three modes: charging, boost, and pumping modes. Each mode will be described individually assuming that the upper phase-leg switch is on. Under these conditions, the potential of the output node is nearly . For convenience, the

0885-8993/$20.00 © 2005 IEEE

PARK AND JAHNS: SELF-BOOST CHARGE PUMP TOPOLOGY | 301

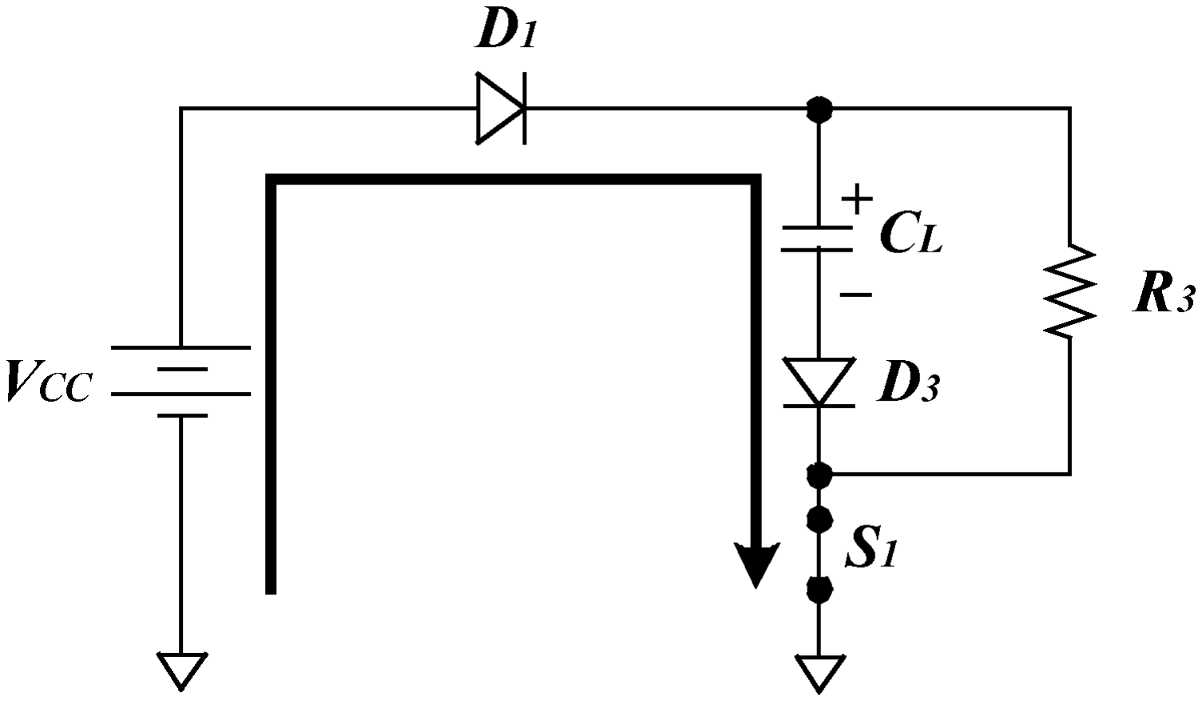
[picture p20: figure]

Fig. 2. Charging mode (S is on and S is off).

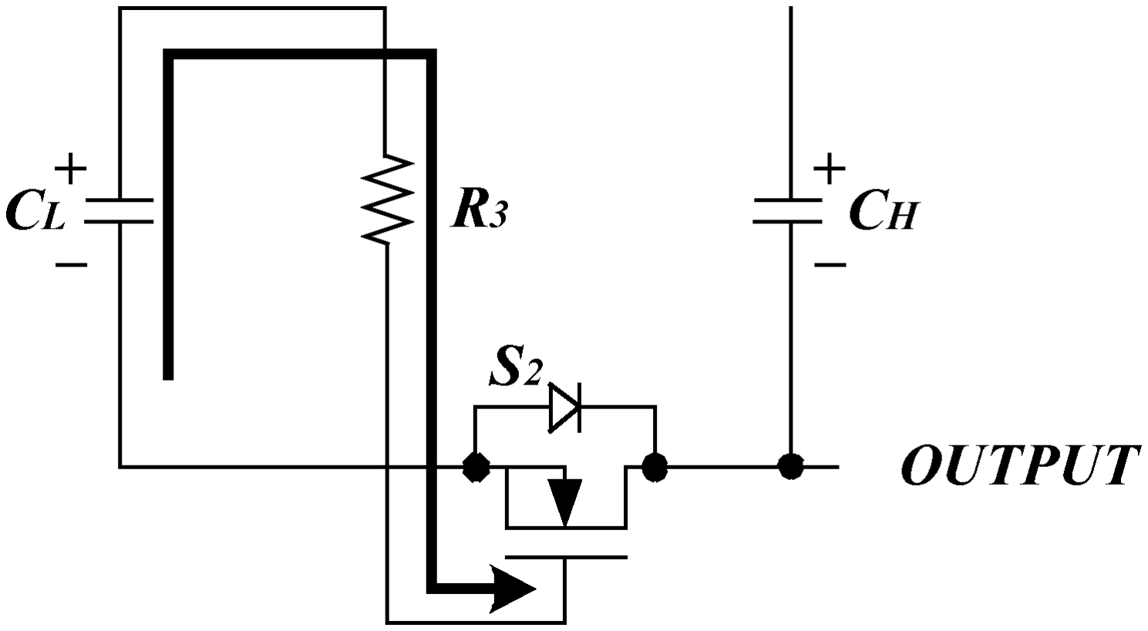
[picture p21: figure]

Fig. 3. Boost mode (S is off and S is active).

negative rail is considered to be ground potential in the following description.
Charging Mode (Fig. 2): The boost capacitor | in Fig. 1 is
charged by the single low-side power supply | through
and | when the switch | turns on as shown in Fig. 2. | and
remain in their off-states since the gate-source voltage
is forced to | during this charging mode. | , | , | and
must all be high-voltage devices that can sustain voltages
up to the dc link voltage | . | can be a low-voltage diode
because its maximum reverse voltage is limited by the voltage
on | which is lower than | . A Schottky diode is preferred
for | in order to minimize its voltage drop and the resulting
conduction losses.
Boost Mode (Fig. 3): When | turns off, the voltage | on
the boost capacitor | starts to charge the gate capacitance of
, | , through | . Assuming that | is much bigger than
, the decrease in the | voltage | is negligible. The
value of | determines the turn-on time of | , but does not
affect the magnitude of the final | gate voltage. Once
is charged, there is no additional current flow or loss in | .
The voltage at the negative (lower) terminal of | rises from
ground level to | (the output node voltage) as switch | turns
off and the drain-source voltage of | decreases as shown in
Fig. 3.
Pumping Mode (Fig. 4): After | fully turns on, the charge
in the boost capacitor | is transferred to the high-side capac-
itor | that serves as the local supply for the high-side switch
gate. This pumping mode ends when | is turned on again by
the external control. Continuous switching of | insures that
gate drive charge is available at all times to the high-side switch without any interference with the desired phase-leg switching sequence.
C. Paper Organization

Models for each of the three modes are analyzed in Section II using linearized diode and metal oxide semiconductor field ef-

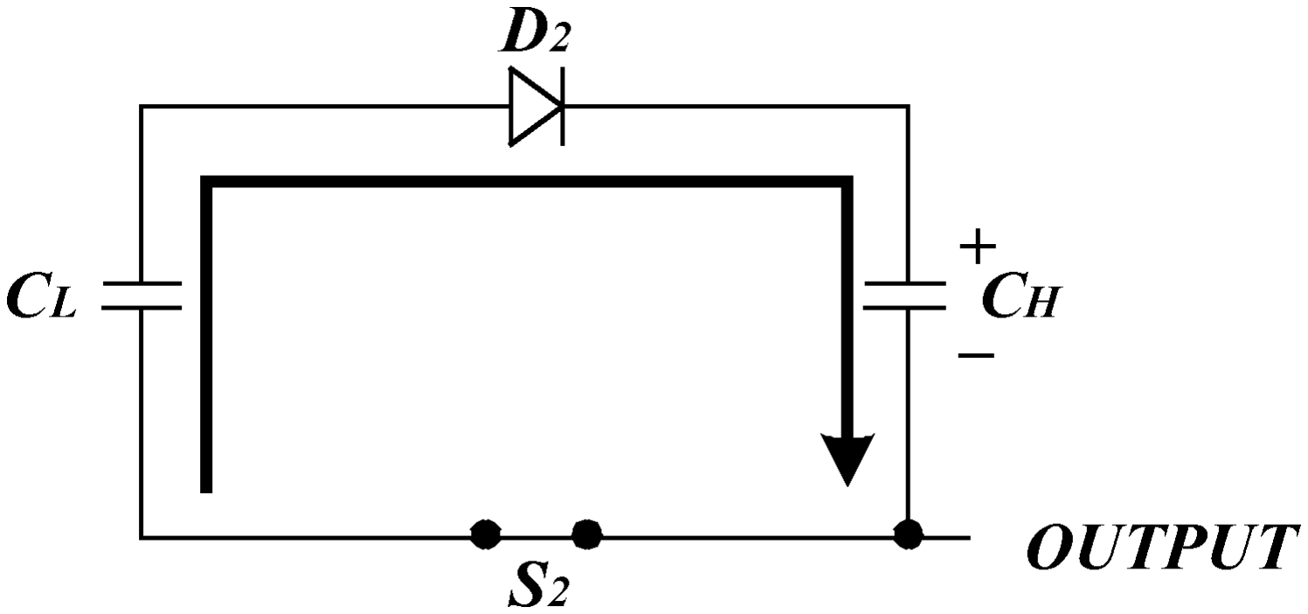
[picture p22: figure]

Fig. 4. Pumping mode (S is off and S is on).

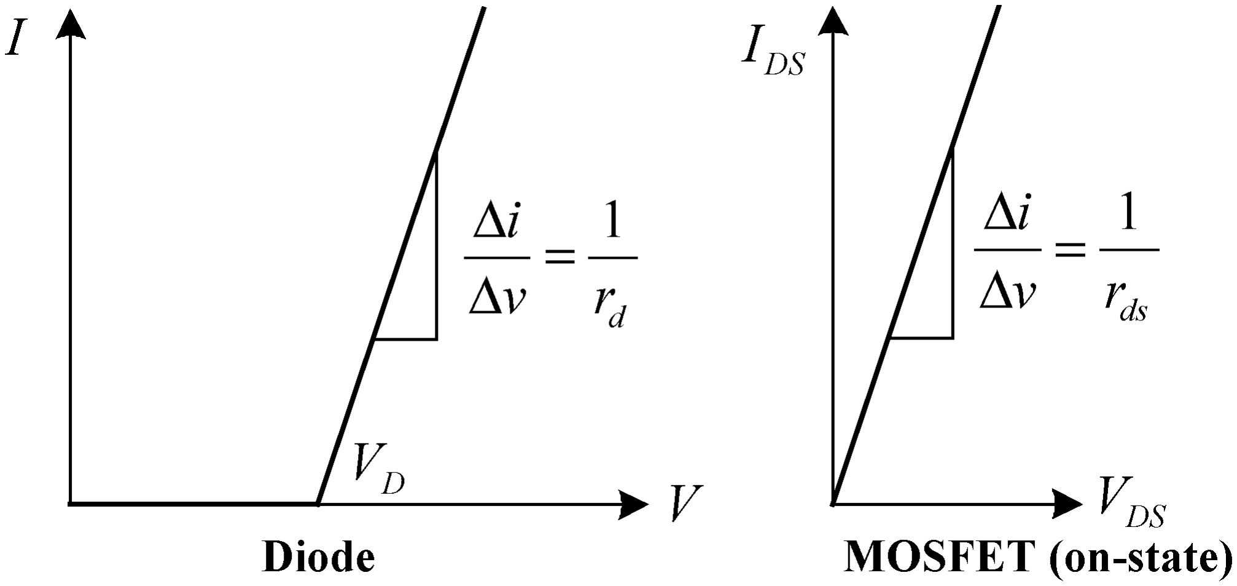
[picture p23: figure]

Fig. 5. Linearized diode and MOSFET models.

fect transistor (MOSFET) models that include the effects of load current. For high voltage applications, the voltage drops caused by the internal resistances of the diodes and MOSFETs become progressively more significant as their current levels increase. Steady-state operation is also analyzed, illuminating the effects of important parameters including frequency, duty cycle, delay times, and switching times. Following this analysis, simulation and experimental results are presented in Section III to verify the model and to demonstrate the circuit’s operating characteristics.

II. CHARGE PUMP CIRCUIT ANALYSIS

Fig. 5 shows the voltage-current characteristics of a common piecewise-linear model for diodes and on-state MOSFETs that will be used in this simplified analysis. The V-I characteristics of the diode can be defined by two parameters—the voltage drop
and the on-state resistance | .
As note above, a Schottky diode is a good choice for | in
order to minimize its forward voltage drop. The Schottky diode forward voltage is typically 0.1 0.2 V, while the comparable voltage for a standard silicon junction diode is 0.7 V.
The MOSFET will be modeled as a simple resistor after it turns on as shown in Fig. 5. The reverse leakage current of the MOSFET and diode are ignored in this analysis. IGBT’s could be used instead of MOSFETs for a high-voltage application ( 600 V), but the forward voltage drop of an IGBT is typically higher than that of a MOSFET for low current conditions. The voltage waveforms across each low-side and high-side capacitor during the three operating modes are shown in Fig. 6 for initial start-up operation. The fixed-frequency input control
signal | and the switch | drain-source voltage | are
also shown to help explain the circuit’s operation.
The equations for the boost capacitor | voltage | and
the high-side capacitor | voltage | will be analyzed for
each of the three operating modes using equivalent circuits. The
value of | under steady-state conditions will also be calcu-

302 | IEEE TRANSACTIONS ON POWER ELECTRONICS, VOL. 20, NO. 2, MARCH 2005

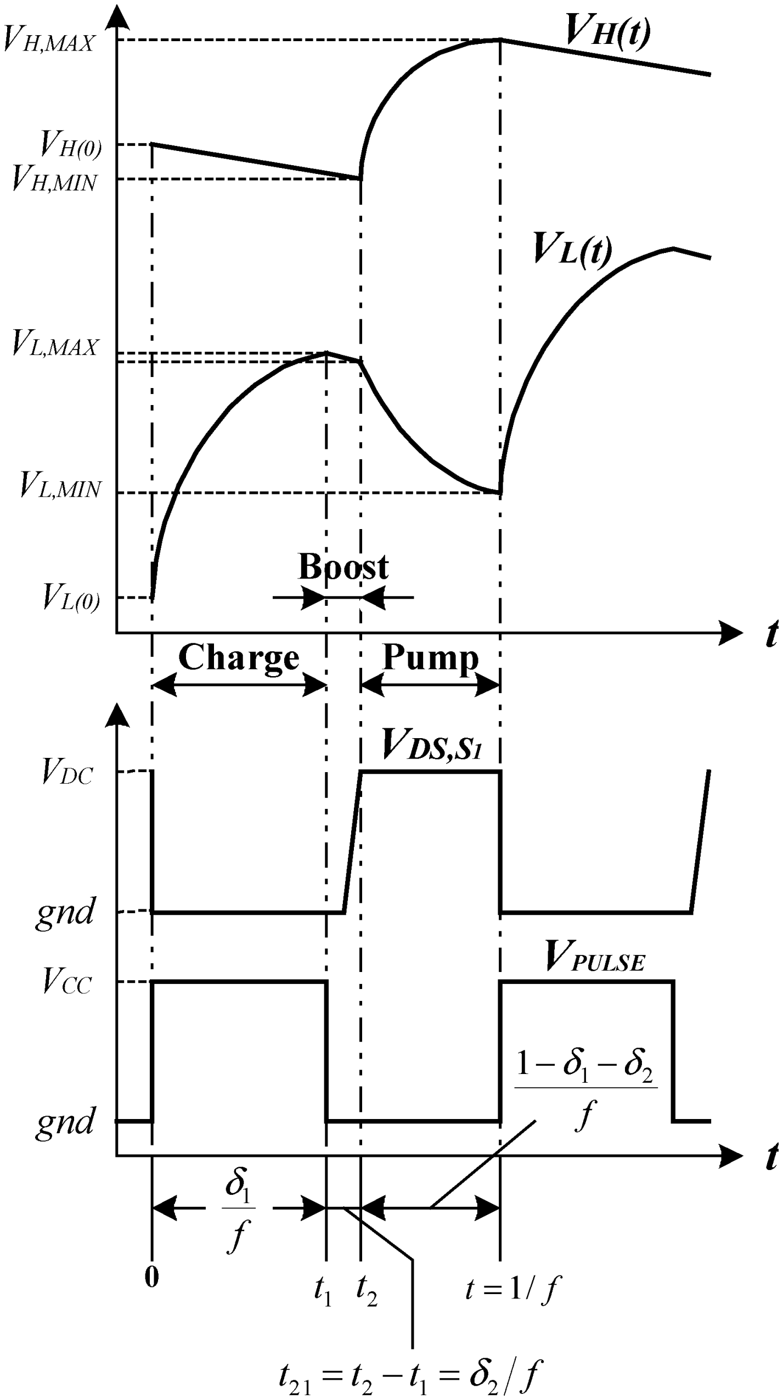
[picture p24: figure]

Fig. 6. Self-boost charge pump waveforms during initial start-up operation.

lated as a function of the boost time to illustrate the control principles for the new charge-pump circuit.

A. Charging Mode Equivalent Circuit and Analysis
During the charging mode, switch | is on and switch
is in its off state. The boost capacitor | is charged through
, | and | . The equivalent circuit for the charging mode
is shown in Fig. 7. The maximum charging voltage of | is
and the equivalent resistor value
is | . The boost capacitor voltage
during the charging mode can be calculated as

(1)

It is worth noting that the same voltage | (plus the
diode drop) appears across resistor | during the charging
mode, resulting in power dissipation in | during this interval.

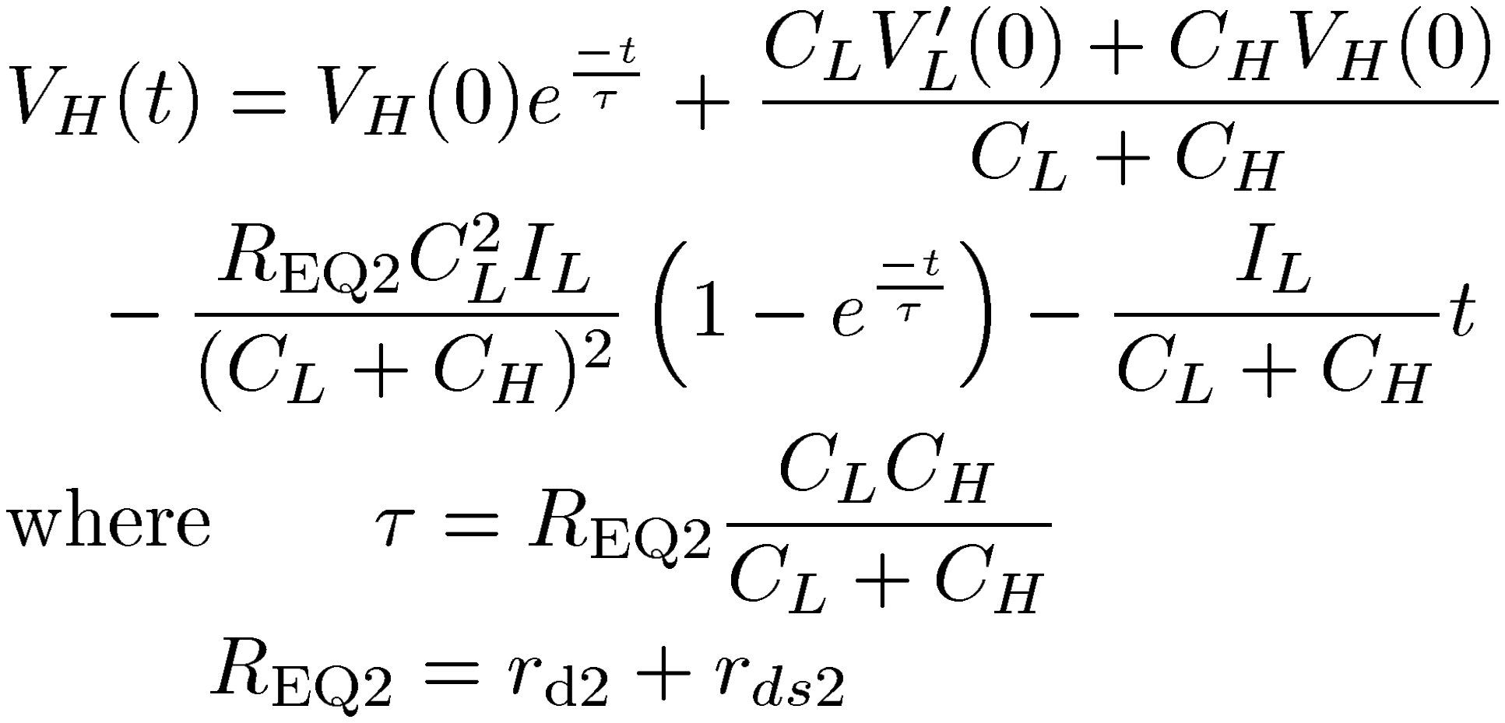
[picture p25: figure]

B. Boost Mode Equivalent Circuit and Analysis
During the boost mode, | turns off, | transitions to its off-
state, and the gate capacitance of | is charged so | begins to
turn on. Fig. 8 shows the equivalent circuit during this operating mode. The time constant of the exponential voltage increase is

(2)

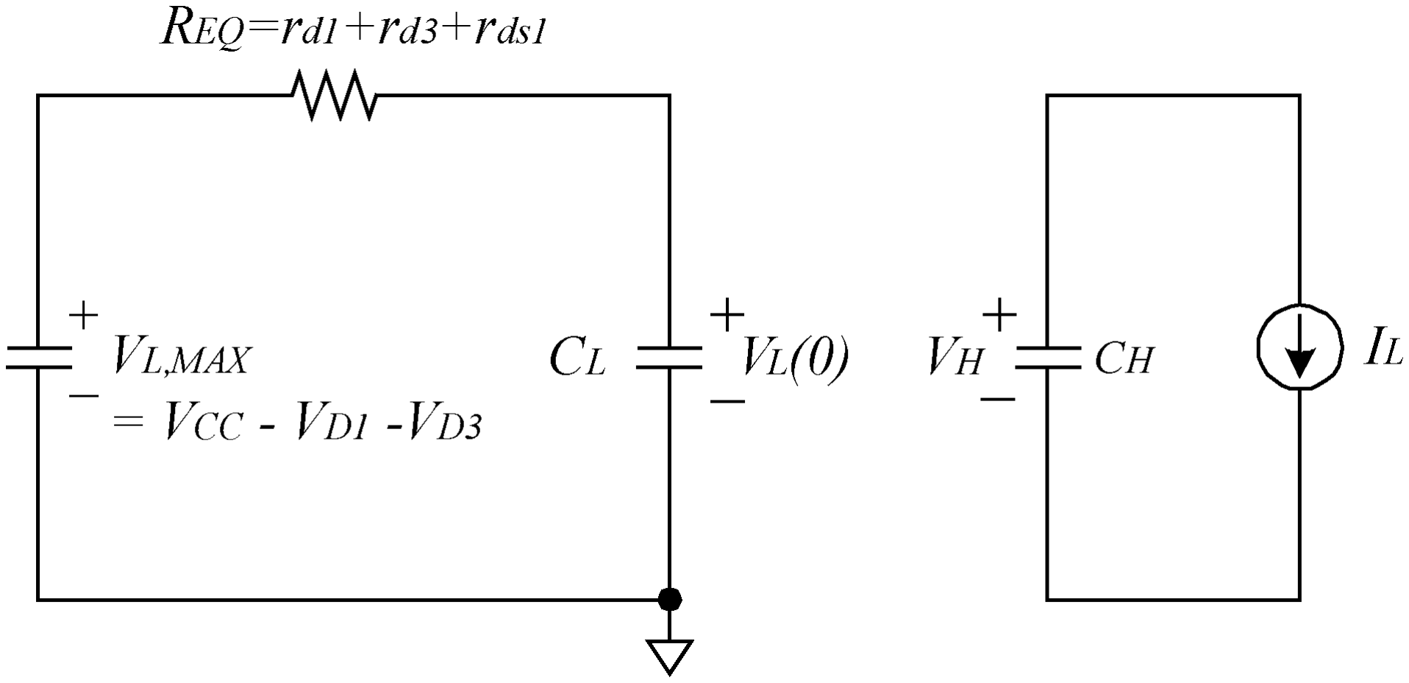
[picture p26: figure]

Fig. 7. Charging mode model.

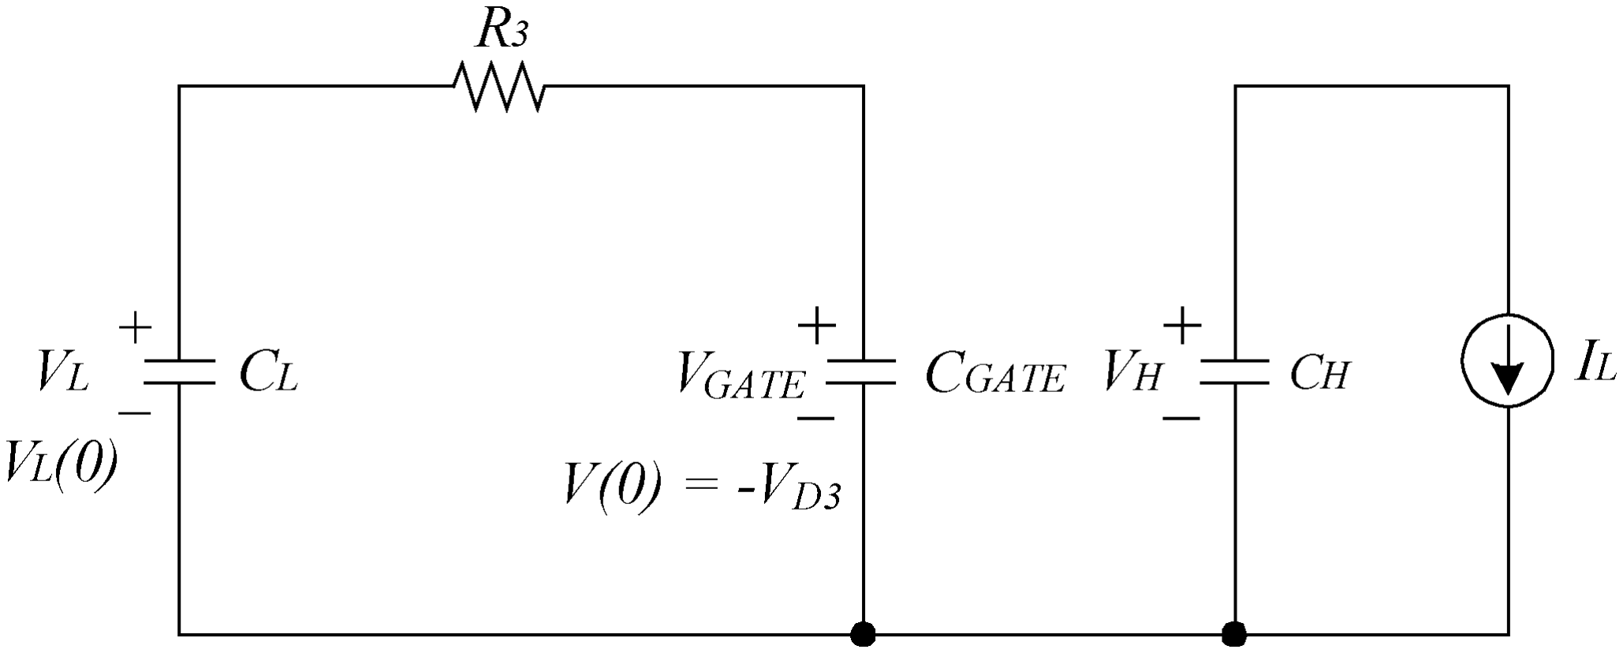
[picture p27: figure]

Fig. 8. Boost mode model.

where | is the total gate capacitance of | .
The voltage on both | and | following completion of
this gate-charging interval is

(3)

It is evident in (3) that if | is much bigger than | , the
voltage decrease of | compared to its initial value | is
negligible, and the value of | does not affect the final voltage
value.
The load on the gate drive circuit is modeled by a constant
load current | that flows at all times. The floating high-side ca-
pacitor | is discharged by this load current | during both the
charging and boost modes. Thus, the equation for the high-side capacitor voltage during the boost mode can be expressed simply as

(4)

C. Pumping Mode Equivalent Circuit and Analysis

The pumping mode begins when fully turns on while remains off. The equivalent circuit for this pumping mode is
shown in Fig. 9, where the equivalent resistance | consists
of the series combination of the equivalent resistances of diode
and switch | . The high-side capacitor voltage
can be derived as

(5)

(6)

(7)
(8)

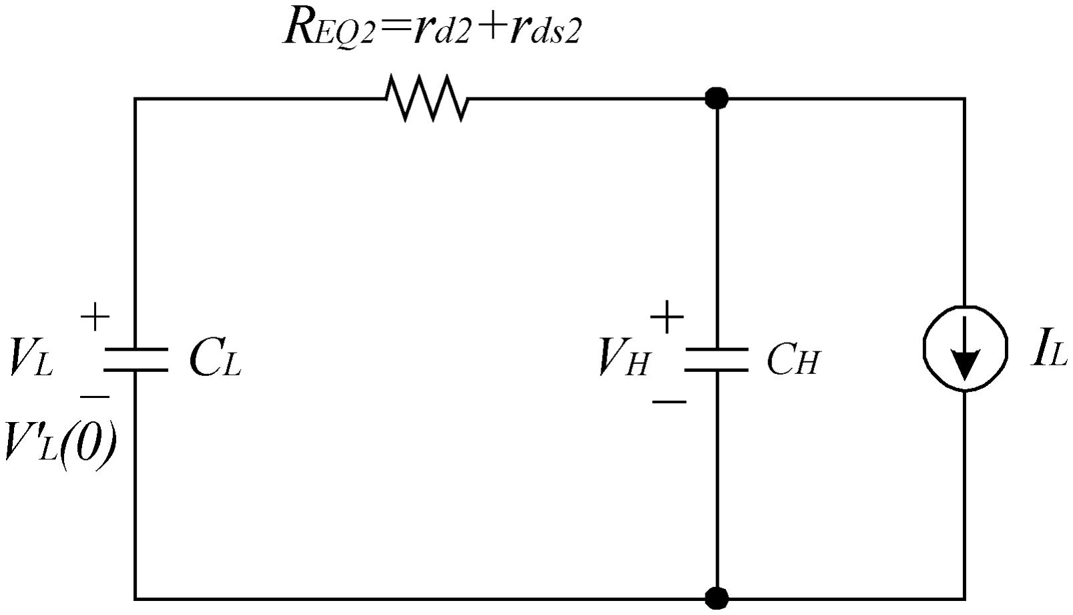
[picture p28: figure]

Fig. 9. Pumping mode model.

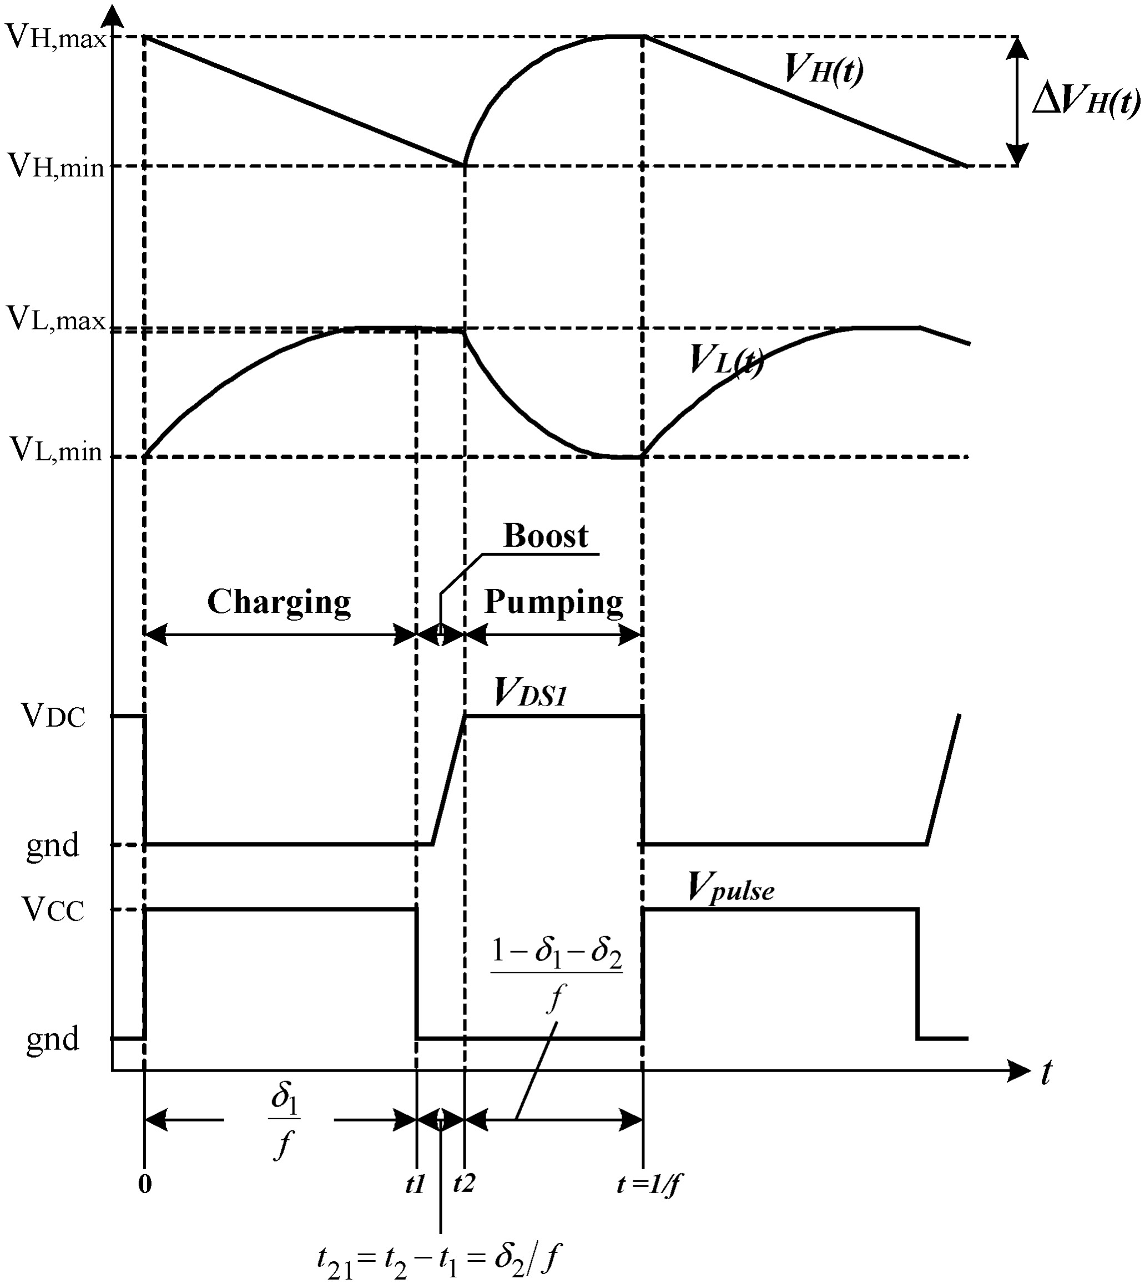
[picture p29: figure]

Fig. 10. Self-boost charge pump waveforms during steady-state operation.

The second term in (5) represents the stored capacitor charge in that is transferred from the low-side supply to the high-side gate drive. The third and fourth terms represent the voltage drops due to the equivalent resistor and the gate drive load current, respectively.

D. Under Steady-State Conditions

Under steady-state conditions, the maximum and minimum
voltage levels of | and | remain constant as shown in Fig. 10.
Applying the steady-state constraints, the minimum value of the high-side capacitor voltage during steady-state conditions can be expressed as

(9)

where | (10)

and the duty cycle values during the charging and boost intervals
are | and | , respectively (see Fig. 10).
In (9), the second term represents the ripple voltage amplitude . In order to reduce the ripple voltage amplitude, either the
value of the high-side capacitance | must be increased or a
higher frequency | is required. However, the switching losses
in switches | and | make it undesirable to raise the frequency
too high. Reducing the duty cycle interval | makes it possible
to transfer more charge from the low to high sides, and this helps to reduce the ripple voltage amplitude. However, it is important
to recognize that one of the most direct ways to reduce | is to
lower the value of resistor | which causes higher power dissi-
pation in | during the charging mode. As a result, selection of
the | value represents of the significant tradeoffs that must be
considered during the circuit design process.
can be derived starting from (5), defining the duration of the pumping interval as
(see Fig. 10). If | , the value of the exponential
function in this equation is less than 0.14 | . Assuming
that this condition is met so that the terms proportional to this exponential can be ignored, (5) can be evaluated at the end of the pumping interval to establish an approximate expression for

(11)

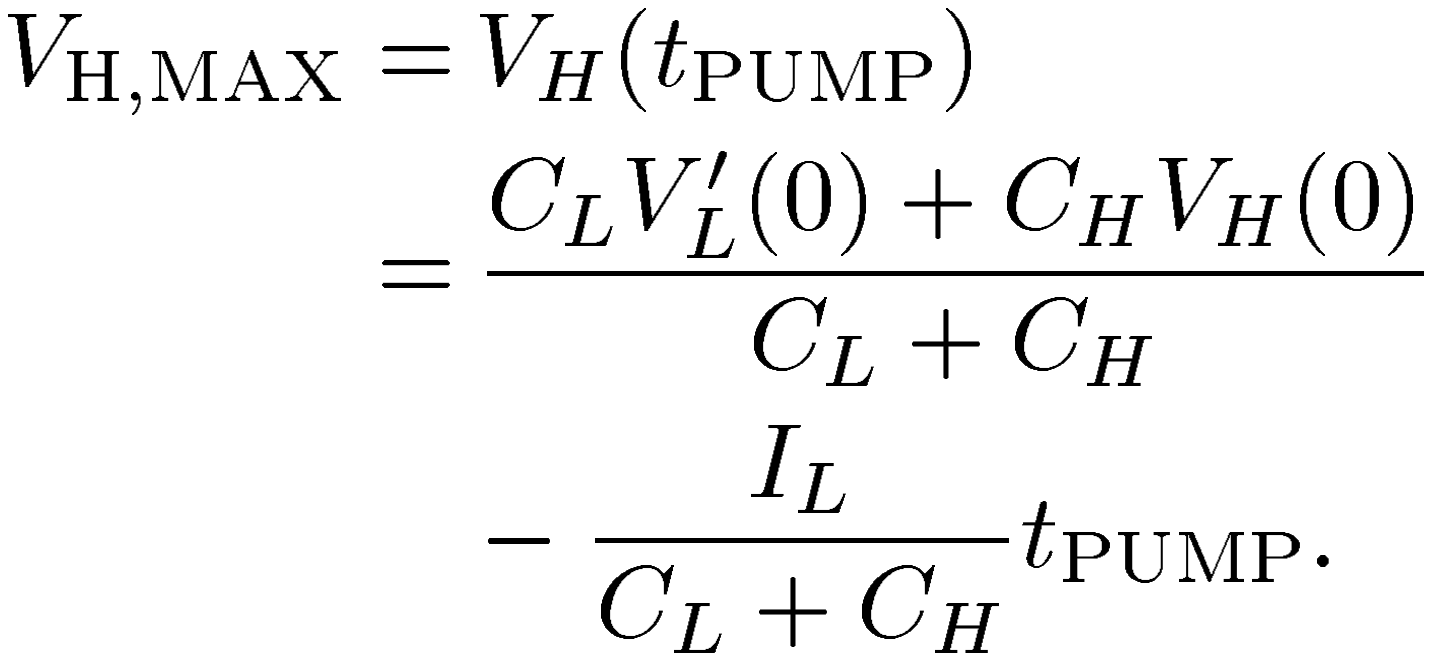
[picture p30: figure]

The final expression of | can be derived using the fol-
lowing two initial conditions at the beginning of the pumping
stage using the previously-defined variable | and (9) and
(10)

(12)

(13)

Substituting these two expressions into (11) and solving for leads to

(14)
Equation (14) is valid only if the durations of the charging and pumping modes are sufficiently long compared to the time constants during each of these intervals. If not, the maximum value of decreases and the exact value of should be calculated using (5). If possible, the time constants in
(1) and (6) should be set to values that are small compared to the charging and pumping time intervals for a given frequency condition. Otherwise, the maximum output voltage decreases due to insufficient charging and pumping times. Although this sug-
gests reduced values for | and | , higher capacitance values
are required to minimize the voltage ripple [see (10)] and to
increase the maximum value of the output voltage | in
(14). This identifies another significant tradeoff that must be addressed during the circuit design process.
E. Calculation of Boost Time

As the operating frequency increases, the effect of the boost time (see Fig. 6) on the output voltage is more significant be-

304 | IEEE TRANSACTIONS ON POWER ELECTRONICS, VOL. 20, NO. 2, MARCH 2005

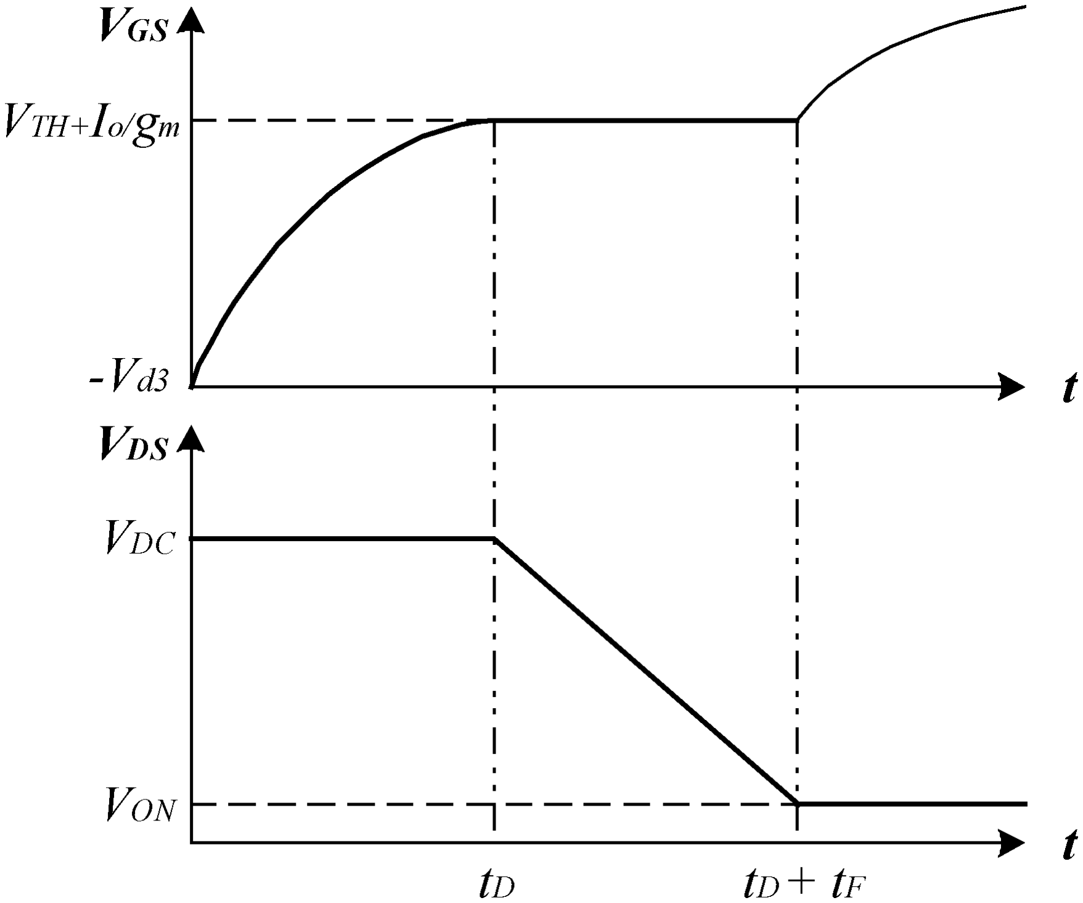
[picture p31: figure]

Fig. 11. V | and V | waveforms for S during t | boost interval.

cause the ratio of charging (pumping) to discharging time values
for | decreases if | and duty cycle | are fixed in value. It
should be noted that | is determined by the boost-mode time
constant | defined in (2). The duration of the boost mode
does not change as the frequency | is varied for a given switch
and a given value of | . This makes | a key parameter
under higher frequency conditions since duty cycle | is directly
proportional to the frequency (i.e., | ).
Closer examination reveals that the time interval | can be
separated into two subintervals consisting of a delay time | and
fall time | , representing the typical turn-on switching charac-
teristics of | as shown in Fig. 11. During | , the gate node
is charged up to the threshold voltage | . At that point, the
drain current starts to flow in | . | falls during | while the
gate-source voltage | remains nearly constant at | due to
the Miller effect.
The intervals | and | can be calculated using the circuit
and switch model parameters as follows [7]:

(15)

(16)

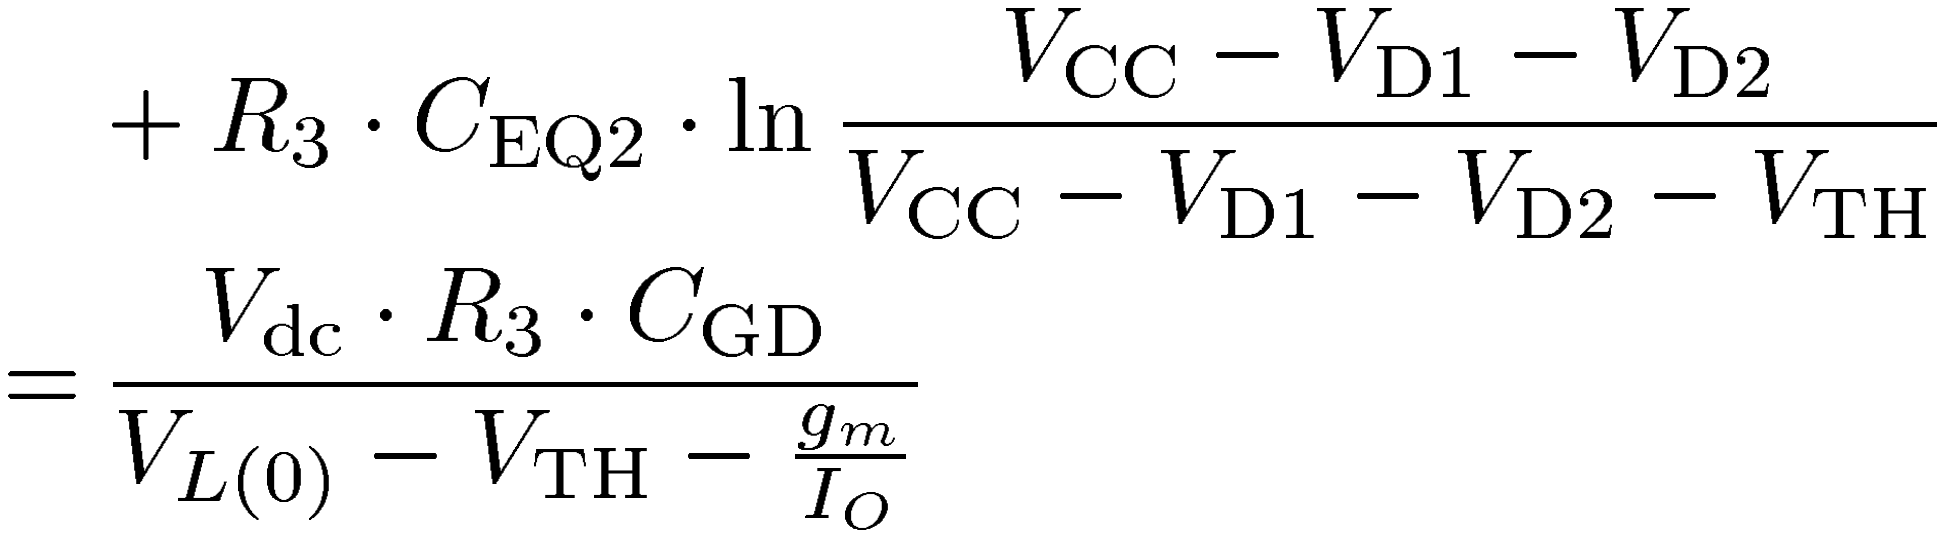
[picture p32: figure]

where
gate threshold voltage | ;
dc link voltage | ;
device transconductance | ;
load inductor current

(17)

device gate-drain capacitance | ;
device gate-source capacitance | .
It should be no surprise that choosing a MOSFET for that has fast switching characteristics, including low values of and , helps to reduce the duration of the boost interval

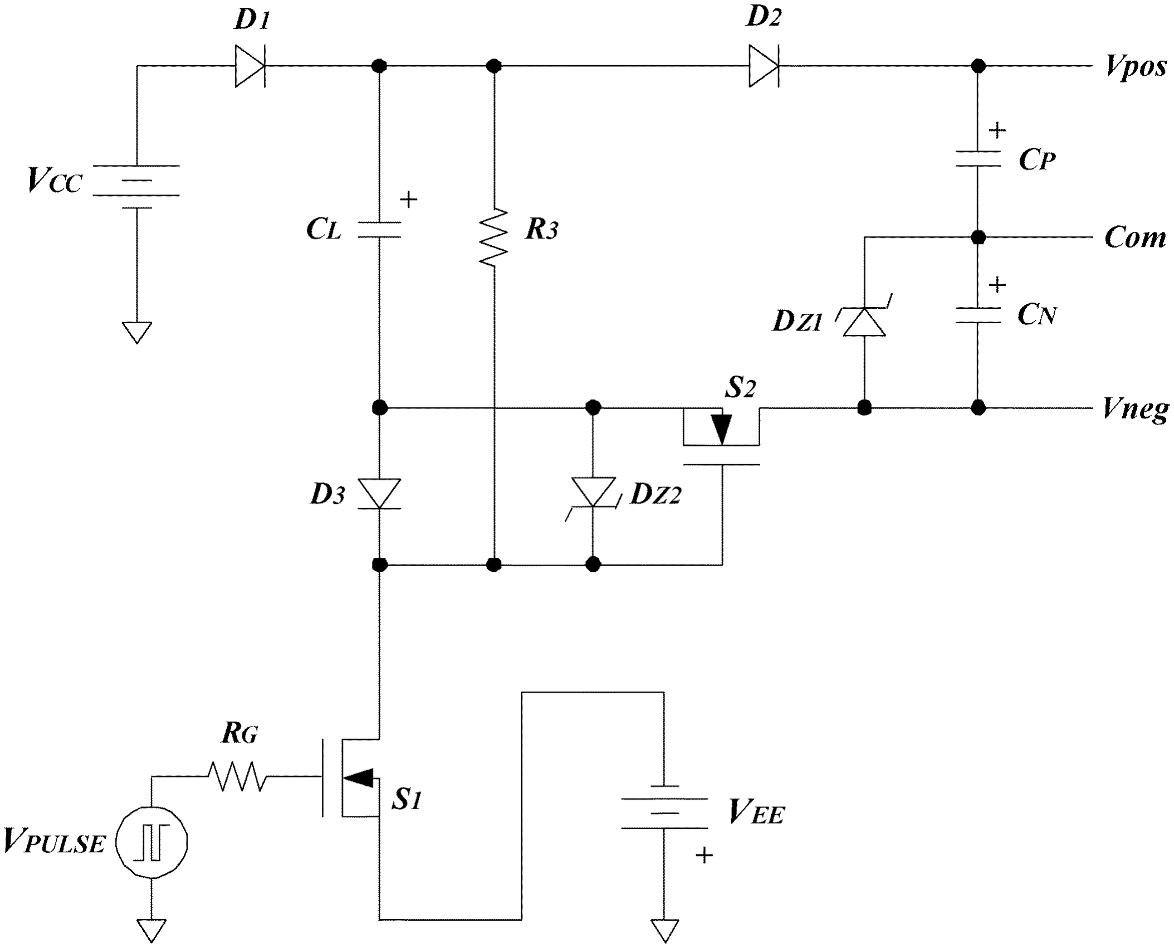
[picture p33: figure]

Fig. 12. Modified self-boost charge pump with positive- and negative-bias voltage supply capability.

by reducing the delay and fall times | and | . In addi-
tion, (15)–(17) indicate that reducing the values of | and
also help to reduce | . However, the performance tradeoffs in-
volved in lowering the values of these two circuit component values have already been noted and will be discussed further in Section II-G.
F. Circuit Modifications for Bipolar Gate Voltages

Negative gate bias is widely used in high-power phase-leg applications in order to prevent dangerous retriggering problems. Fig. 12 shows a modified version of the self-boost charge pump scheme with positive and negative voltage supply capa-
bility. Zener diode | , positive voltage capacitor | , and neg-
ative voltage capacitor | are used to split the boost capac-
itor voltage | into two parts for the high-side gate drive. The
second supply voltage | is added to provide negative gate
voltage for the low-side switch in the phase leg. The ground terminal in this figure corresponds to the low-side dc bus voltage, consistent with Fig. 1.
During the charging mode, boost capacitor is charged by in order to develop nearly the same positive and neg-
ative voltages ( | and | , respectively) in the high-side gate
drive. The maximum charging voltage of | is
. Zener diode | is required to insure
that the maximum safe gate-source voltage of | is not exceeded
during the boost or pumping modes. During the pumping mode,
stored charge in | is distributed to both | and | , with the
negative-bias voltage developed across | limited by | .
The zener diode | should be selected with a clamping
voltage | that is less than | in order to maintain a stable
negative bias voltage source for the high-side switch under all
operating conditions. If the clamping voltage | is higher
than | , the negative-bias gate voltage for the high-side switch
will drop to the lower voltage | when the low-side switch
is on. This occurs because the Com terminal in Fig. 12, corresponding to the low-side switch collector voltage (see Fig. 1), falls to nearly ground (i.e., low-side dc bus) potential when the low-side switch is on.
Using (14), approximate expressions for the negative-bias voltage and the maximum positive-bias voltage
under steady-state conditions can be derived as

(18)

(19)

G. Circuit Design Guidelines

In order to minimize cost and complexity, the high-side power supply uses a simple open-loop control to set the output voltage with a fixed-frequency, fixed duty-cycle switching sequence. The desired output voltage characteristics can be specified in terms of the maximum output voltage and ripple voltage amplitude for a specified load current. These target
values for | , | , and | provide the necessary starting
points for determining values for the circuit components.
Once these three performance parameters are set, tradeoffs between the sizes of the circuit components (influencing cost) and the circuit losses come to the forefront in determining the circuit component values. This tradeoff is particularly apparent when considering the voltage ripple requirement. Equation (10)
indicates that product of | and frequency | must be approx-
imately constant in order to achieve a particular value of ripple
voltage | for the specified load current | . (It is assumed
that the sum of the duty cycles | can vary over only a
rather narrow range in the vicinity of 0.5.) Increasing capaci-
tance | increases the capacitor’s size and cost, while raising
the frequency | increases the circuit losses because of higher
total switching losses in | and | .
In addition, increasing frequency | will likely make it nec-
essary to reduce the value of resistor | , further increasing
circuit losses, as described previously. As a general guideline,
the value of | should be chosen so that the boost interval duty
cycle | does not exceed 0.1 at the desired operating frequency.
Higher values of | are likely to unacceptably degrade the
charging times for capacitors | and | during the charging
and pumping modes, respectively. The average power loss in can be calculated approximately by assuming a 50% duty
cycle (i.e., | ), leading to the following expression:
| | | (20)

Another factor that must be considered in the process of selecting the operating frequency is the quality of the MOSFET
switches | and | . Better MOSFETs with lower values of
on-state resistance | , lower gate capacitance [ | in (2)],
and faster switching speeds will reduce circuit losses and make it considerably easier to raise the frequency . However, adoption of such improved devices is likely to increase the MOSFET size and cost.
Ultimately, selection of the frequency depends on the application. For example, if the target application calls for integrating the high-side power supply inside a power module, then minimizing the volume of the capacitor components is likely to be a high priority. In this case, the design approach would likely call for raising the operating frequency as high as possible, limited by the maximum losses that can be safely dissipated inside the module.
Up to this point, it has been assumed that the value of the charging mode duty cycle is 0.5. This is a reasonable choice because of the need to charge and discharge low-side capacitor
each cycle. In fact, a simple timer circuit may force | to
be fixed at 0.5. However, further tuning the value of | (when
practical) may yield some improvement in circuit performance by providing a means to compensate for the impact of the boost duty cycle and differences between the time constants for the charging and pumping intervals [see (1) and (5)].
The selection of capacitance of also involves tradeoffs between competing objectives of performance and size/cost. In
particular, increasing capacitance | tends to increase the peak
value of the output voltage | for a given value of supply
voltage | because of the importance of the last term in (14).
The penalty is a larger capacitor. Considering these tradeoffs, a
good starting point is to choose | and | to be equal in value,
resulting in time constants for the | charging and discharging
(i.e., pumping) intervals that have similar values.
Assuming that the conditions are met for (14) to give a good
approximation of | , (14) can be used to eliminate load
current | and frequency | from the expression. If one accepts
the observation that the next-to-last term in (14) can typically be ignored because it is small compared to all of the others, the equation can be rearranged to yield an approximate expression for the supply voltage needed to achieve the specified value

(21)

III. SIMULATION AND EXPERIMENTAL RESULTS

Simulations and experimental tests were carried out to verify the operation of the self-boost charge pump circuit. Fig. 13 shows the test circuit that was used for the laboratory tests. The simulations have been carried out using PSPICE with the same test circuit. The devices used for the switches and are both the same MOSFET type BUZ50B manufactured by Infineon and rated at 1000 V and 3 A. Diode types 1N4007
and 1N5818 were selected for the high-voltage diode | and
the low-voltage Schottky diode | , respectively. The reverse
blocking voltage of the 1N4007 diode is 1000 V, the same as the MOSFET voltage rating.
The test conditions used for both the experimental tests and the simulations are as
V | V
F | F | k
k
The value of | was set to 600 | to adjust the load current
to approximately 28 mA for a | value of 17 V. This resistor
represents an average load of 476 mW imposed by the high-side switch gating. For reference, this power level would be sufficient for use with commercially-available gate drive ICs to drive a

306 | IEEE TRANSACTIONS ON POWER ELECTRONICS, VOL. 20, NO. 2, MARCH 2005

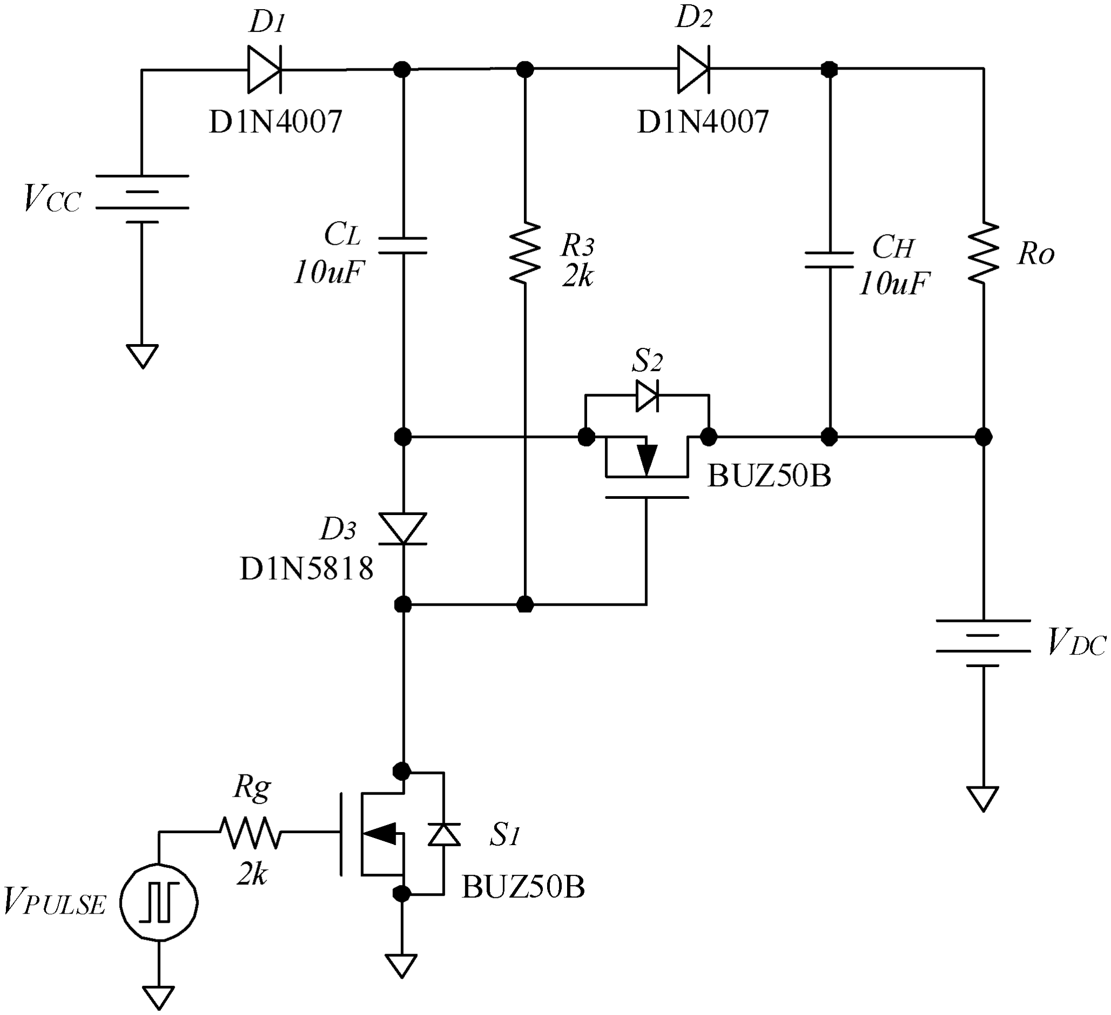
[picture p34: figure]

Fig. 13. Self-boost charge pump test circuit.

1200-V IGBT with a 100-A current rating at frequencies in the 10–20 kHz range [8].
The ripple voltage can be calculated from (10)

V (22)

The sum of the charging- and boost-mode duty cycle values is assumed to be 0.6 (i.e., 0.1) based on the selected circuit design values.
Rearranging (21), the maximum high-side output voltage can be approximately calculated to be

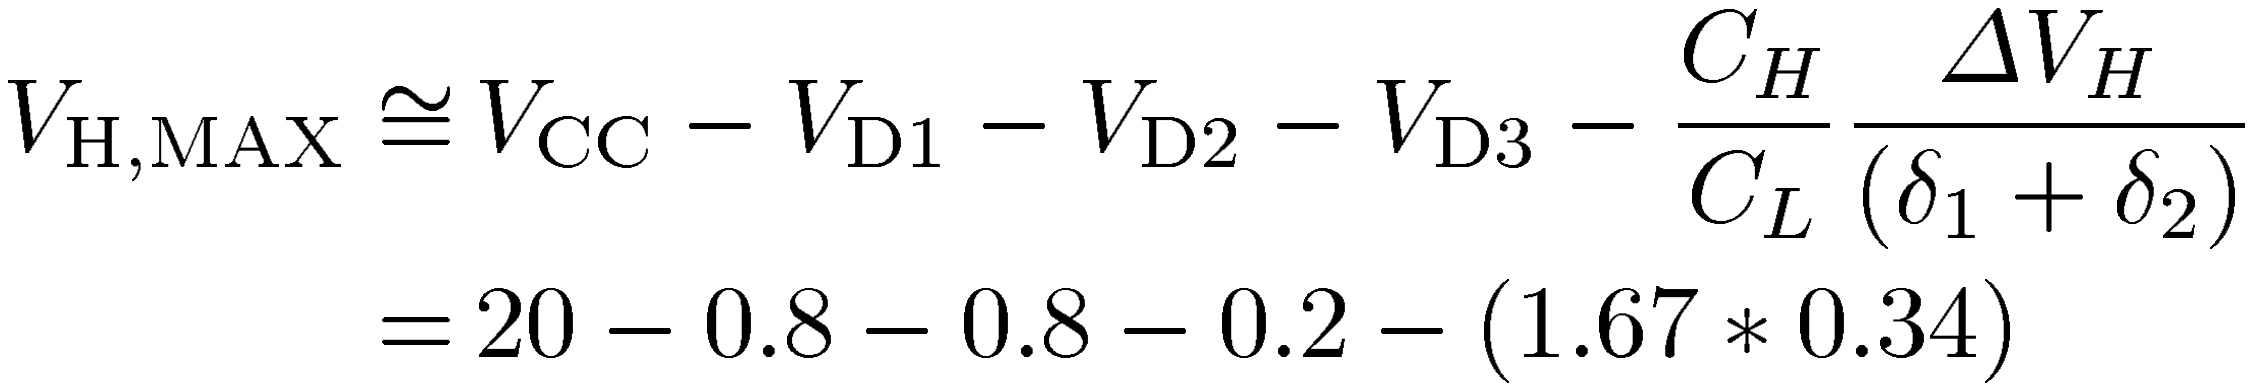
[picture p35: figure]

| V | | (23)
where it is assumed that the | V and
V because | and | are high-voltage diodes and | is a
Schottky diode.
Fig. 14 shows experimental waveforms and overlaid simula-
tion results for the input control voltage | , the high-side
capacitor voltage | , and the switch | drain-source voltage
under steady-state conditions. The measured value of
the ripple voltage | is approximately 0.4 V which is small
enough to insure robust performance of the high-side gate drive.
The calculated maximum capacitor voltage | and
ripple voltage | values demonstrate satisfactory agree-
ment with the measured values ( | V and
V). The simulated and experimental waveshapes also exhibit good agreement, although the measured waveform in Fig. 14 exhibits a small sudden downward step at the beginning of the charging mode that is not predicted by the simple analysis presented above. The amplitude of this step is approximately 0.1 V, nearly equal to the difference between the calculated and measured values of . Investigation has revealed that this voltage step is caused by the reverse recovery

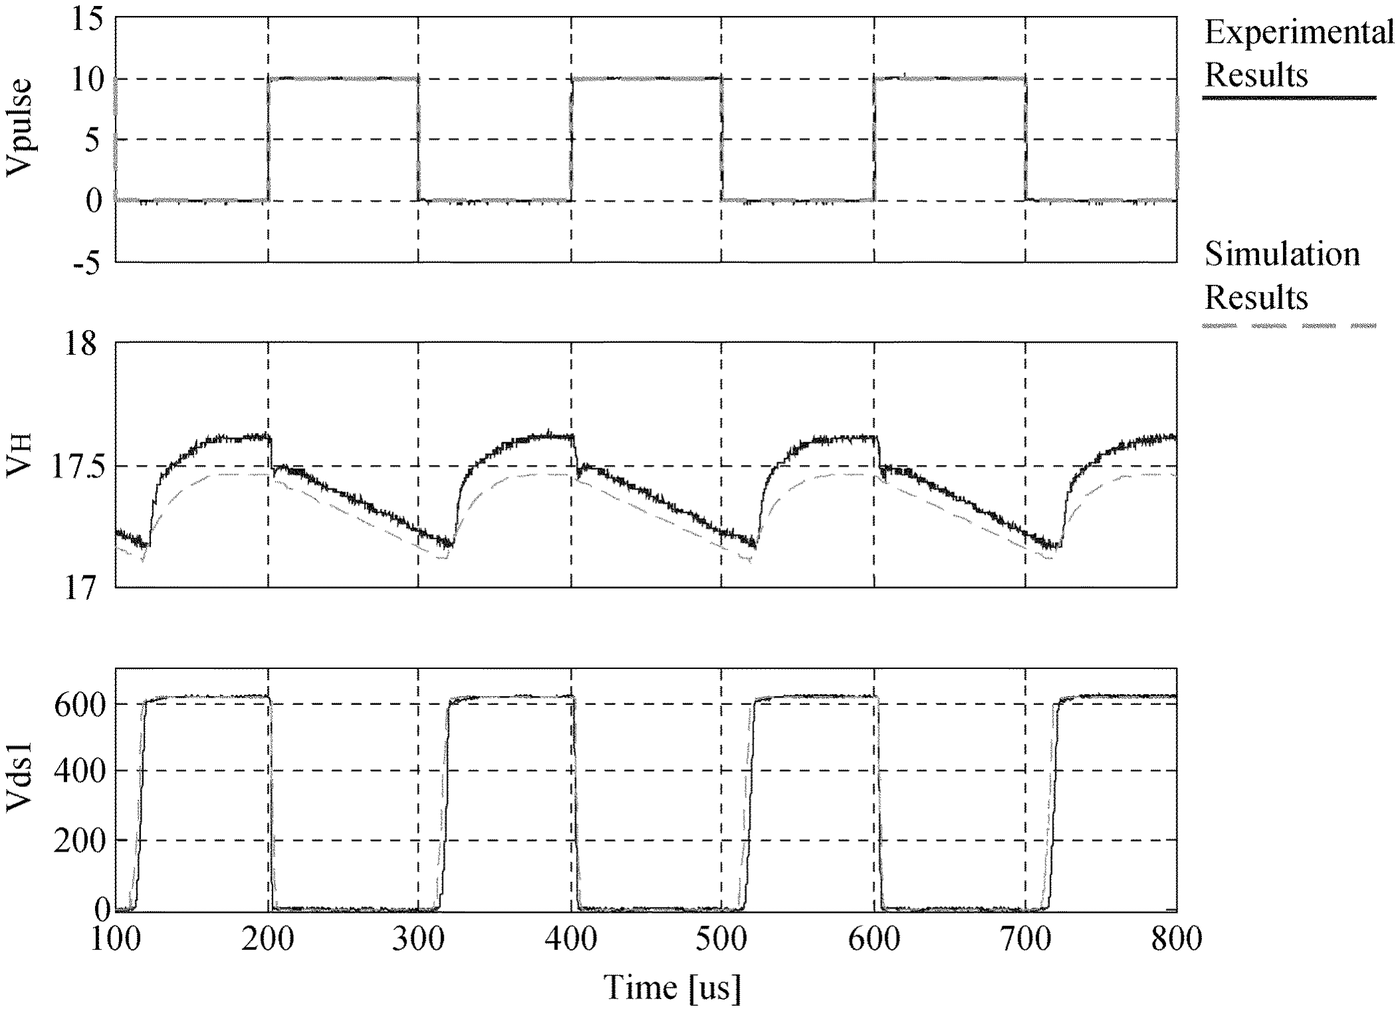
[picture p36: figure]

Fig. 14. Simulation and experimental results for V | , V , and V | .
current of diode | when | turns on. Stored charge in
is transferred to | during the | reverse recovery interval,
resulting in the observed voltage step. This diode reverse recovery characteristic is not been included in the simulation model, so the voltage step does not appear in the simulated waveform in Fig. 14.
The value of the | turn-on interval | can be measured di-
rectly from the experimental waveforms in Fig. 14 to be ap-
proximately 20 s. Even though the duty cycle of | (i.e.,
) is set at 0.5, the actual duty cycle of the | charging in-
terval | is approximately 0.4, meaning that the
boost-mode interval reduces the charging duty cycle by approximately 20% (from 0.5 to 0.4). Reducing the value of
would cause the ripple voltage amplitude | to decrease, but
the penalty of higher losses in resistor | must be considered
as discussed previously in Section II. The average power dissipation in resistor is calculated to be approximately 92 mW using (20) compared to the delivered high-side output power of 476 mW.

IV. CONCLUSION

This paper has described a new self-boost charge pump topology for a floating high-side gate drive power supply. This new power supply circuit provides the following attractive features compared to conventional techniques:
1) robust gate drive power availability for high-side switch that eliminates phase-leg refresh switching requirements even if the high-side switch is permanently on;
2) simple charge-pump configuration requiring no high-frequency magnetic components;
3) high steady-state current supply capability for high-performance gate drives;
4) configurable to provide bipolar gate source voltages for high-side switch;
5) compatible with integrated circuit implementation.
A model for each circuit mode has been derived using piecewise-linear device models. Taken together, these models provide useful predictions of both steady-state and transient operating characteristics, as well as valuable insights regarding design considerations. Both simulation and experimental results have been presented to confirm the promising operating characteristics of the self-boost charge pump circuit. Guidelines have been presented to provide assistance with selection of circuit component values for applying this high-side power supply circuit to new applications.

REFERENCES

[1] HW floating MOS-gate drive ICs, in IR Application Note AN-978, International Rectifier Corp., El Segundo, CA.
[2] S. Storti, F. Consiglieri, and M. Paparo, “A 30 A 30 V DMOS motor controller and driver,” IEEE J. Solid-State Circuits, vol. 23, no. 12, pp. 1394–1401, Dec. 1988.
[3] G. D. Cataldo and G. Palumbo, “Double and triple charge pump for power IC: dynamic models which take parasitic effects into account,” IEEE Trans. Circuits Syst., vol. 40, no. 2, pp. 92–101, Feb. 1993.
[4] R. L. Lin and F. C. Lee, “Single-power-supply-based transformerless IGBT/MOSFET gate driver with 100% high-side turn-on duty cycle operation performance using auxiliary bootstrapped charge pumper,” in Proc. IEEE Power Electronics Specialties Conf. (PESC), Jun. 1997, pp. 1205–1209.
[5] G. F. W. Khoo, D. R. H. Carter, and R. A. McMahon, “Analysis of a charge pump power supply with a floating voltage reference,” IEEE Trans. Circuits Syst., vol. 47, no. 10, pp. 1494–1501, Oct. 2000.
[6] , “Comparison of charge pump circuits for half-bridge inverters,” Proc. Inst. Elect. Eng., vol. 147, pp. 356–362, Dec. 2000.
[7] B. J. Baliga, Power Semiconductor Devices. Boston, MA: PWS, 1995, pp. 387–397.
[8] Agilent Technologies, “2.0 amp gate drive optocoupler with integrated desaturation detection and fault status feedback,” HCPL-316J Data Sheet, 1999.

Shihong Park (S’01) received the B.S. degree in electrical engineering from Yonsei University, Seoul, Korea, in 1988, and the M.S. and Ph.D. degrees from the University of Wisconsin, Madison, in 2003 and 2004, respectively.
From 1988 to 1998, he was with Samsung Electronics, Buchen, Korea, as a Senior Power IC Design Engineer. In 2004, he was a Principal Research Engineer with Fairchild Semiconductor Korea, Buchen, Korea. In March 2005, he joined the School of Electrical, Electronics, and Computer Engineering, Dankook University, Seoul. His main research interests are integrated power electronics modules (IPEMs), power ICs and devices for automotive applications, active gate drive topology, and power converter circuit.

Thomas M. Jahns(F’93) received the S.B. and S.M., and Ph.D., degrees from the Massachusetts Institute of Technology (MIT), Cambridge, in 1974 and 1978, respectively, all in electrical engineering.
He joined the Faculty of the University of Wisconsin-Madison (UW-Madison) in 1998 as a Grainger Professor of Power Electronics and Electric Machines in the Department of Electrical and Computer Engineering. He is an Associate Director of the Wisconsin Electric Machines and Power Electronics Consortium (WEMPEC). Prior to coming to UW-Madison, he worked at GE Corporate Research and Development (now GE Global Research Center), Schenectady, NY, for 15 years, where he pursued new power electronics and motor drive technology in a variety of research and management positions. His research interests include permanent magnet synchronous machines for a variety of applications ranging from high-performance machine tools to low-cost appliance drives. From 1996 to 1998, he conducted a research sabbatical at MIT, where he directed research activities in the area of advanced automotive electrical systems and accessories as co-director of an industry-sponsored automotive consortium.
Dr. Jahns received the William E. Newell Award from the IEEE Power Electronics Society (PELS) in 1999. He has been recognized as a Distinguished Lecturer by the IEEE Industry Applications Society (IAS) from 1994 to 1995 and by IEEE-PELS from 1998 to 1999. He has served as President of PELS (1995–1996) and as a Member of the IAS Executive Board from 1992 to 2001. From 2002 to 2003, he was the Division II Director on the IEEE Board of Directors.

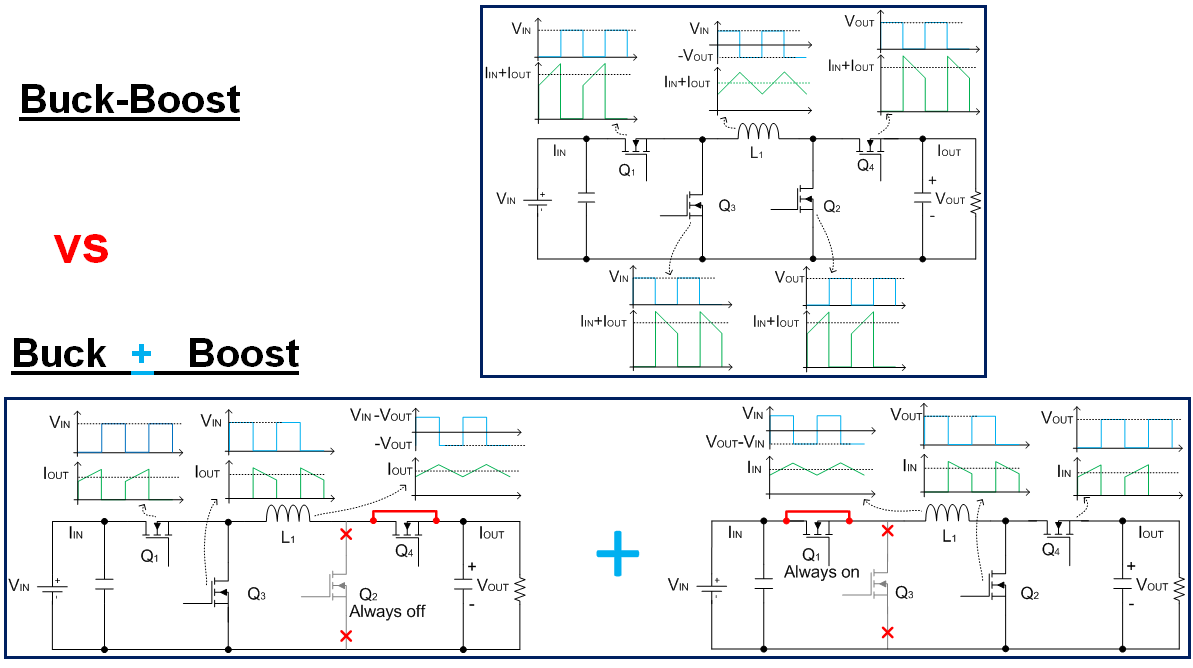
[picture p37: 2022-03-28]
DesignGuide/4SW-BB/TI-Buck-Boost-Modes.png

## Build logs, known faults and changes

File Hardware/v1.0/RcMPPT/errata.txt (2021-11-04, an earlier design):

RcMPPT Hardware Errata Sheet

#1 Buck Converter Module not supplied via diode
	The 5V Buck Converter act like a diode when supplied from the output side
	therefore hindering the output to sink below 5V when supplied only via usb

#2 Unsymmetric supply of the buck converter
	Powerup is only possible when battery is connected

#3 Low side charge pump not connected via 2 diodes
	This shorted buck and boost side together therefore killing the gate drivers

#4 Low side charge pump not cheaper / smaller than boost controller

#5 SBUS not inverted
	SBUS is implemented as inverted UART so it should be inverted on board

#6 Non Bi-Directional Shunt Amplifier
	This makes it hard to detect current flow in the wrong direction and accurate measurements
	at low currents.

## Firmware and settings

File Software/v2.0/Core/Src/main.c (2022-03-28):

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
/* Includes ------------------------------------------------------------------*/
#include "main.h"
#include "adc.h"
#include "crc.h"
#include "dma.h"
#include "hrtim.h"
#include "spi.h"
#include "usb_device.h"
#include "gpio.h"

/* USER CODE BEGIN Includes */
#include "usbd_cdc.h"
#include "usbd_cdc_if.h"
#include "tim.h"
#include "bq76pl536a.h"
/* USER CODE END Includes */

/* USER CODE BEGIN PD */
#define PWR_FLAG_WUF PWR_FLAG_WUF2
/* USER CODE END PD */


/* USER CODE BEGIN PV */
__IO uint32_t Index = 1;
__IO uint32_t ErasingOnGoing = 0;
int new_v_cell_data = 0;

struct BQ76 battery_monitor =
{ .adc_control =
{ .CELL_SEL = CELL_1_6, .TS = BOTH, }, .cb_time =
{ .CBCT = 1, }, .function_config =
{ .CN = CELLS_6, } };
/* USER CODE END PV */

void SystemClock_Config(void);
/* USER CODE BEGIN PFP */
void writeEEPROM8(uint32_t Index, uint8_t data);
void writeEEPROM16(uint32_t Index, uint16_t data);
void writeEEPROM32(uint32_t Index, uint32_t data);

uint8_t readEEPROM8(uint32_t Index);
uint16_t readEEPROM16(uint32_t Index);
uint32_t readEEPROM32(uint32_t Index);
/* USER CODE END PFP */

/**
 * @brief  The application entry point.
 * @retval int
 */
int main(void)
{
	/* USER CODE BEGIN 1 */
	//Set initial EE-Status
	EE_Status ee_status = EE_OK;
	/* USER CODE END 1 */

	/* MCU Configuration--------------------------------------------------------*/

	/* Reset of all peripherals, Initializes the Flash interface and the Systick. */
	HAL_Init();

	/* Configure the system clock */
	SystemClock_Config();

	/* USER CODE BEGIN SysInit */
	LL_HRTIM_StartDLLCalibration(HRTIM1);
	//Enable FLASH Interrupt and set NVIC Priority
	HAL_NVIC_SetPriority(FLASH_IRQn, 0, 0);
	HAL_NVIC_EnableIRQ(FLASH_IRQn);

	//Unlock the Flash write protection
	HAL_FLASH_Unlock();

	//Enable RCC Clock
	__HAL_RCC_PWR_CLK_ENABLE();

	//Init the eeprom
	//If this fails, do an entire chip erase
	ee_status = EE_Init(EE_FORCED_ERASE);
	if (ee_status != EE_OK)
	{
		Error_Handler();
	}
	//Set initial sample rate
	targetSampleDelay = 10000;
	//Set initial Target Voltage
	setTargetVout = 10000;
	targetVout = 0;
	limitIout = 1000;
	//Set initial conversion mode
	conversionState = CONVERSION_STATE_SHUTDOWN;
	//Set initial BuckBoost Band
	buckBoostBand = BUCK_BOOST_BAND - BUCK_BOOST_BAND_HYSTERESIS;
	/* USER CODE END SysInit */

	/* Initialize all configured peripherals */
	MX_GPIO_Init();
	MX_HRTIM1_Init();
	MX_CRC_Init();
	MX_USB_Device_Init();
	MX_TIM5_Init();
	MX_ADC1_Init();
	MX_ADC2_Init();
	MX_TIM1_Init();
	MX_TIM20_Init();
	MX_DMA_Init();
	MX_SPI2_Init();
	/* USER CODE BEGIN 2 */
	LL_ADC_DisableDeepPowerDown(ADC1);
	LL_ADC_DisableDeepPowerDown(ADC2);
	HAL_Delay(1);	//Wait before powering up the regulator
	LL_ADC_EnableInternalRegulator(ADC1);
	LL_ADC_EnableInternalRegulator(ADC2);
	HAL_Delay(1);	//Wait for regulator stabilization
	LL_ADC_StartCalibration(ADC1, LL_ADC_SINGLE_ENDED);
	LL_ADC_StartCalibration(ADC2, LL_ADC_SINGLE_ENDED);
	while (LL_ADC_IsCalibrationOnGoing(ADC1) != 0);
	while (LL_ADC_IsCalibrationOnGoing(ADC2) != 0);
	HAL_Delay(1);	//Wait after calibration before activation ADC
	LL_ADC_Enable(ADC1);
	LL_ADC_Enable(ADC2);
	while (LL_ADC_IsActiveFlag_ADRDY(ADC1) == 0);
	while (LL_ADC_IsActiveFlag_ADRDY(ADC2) == 0);
	HAL_Delay(1);	//Wait before starting conversion
	//Start Timer and ADC Peripherals
	LL_ADC_INJ_StartConversion(ADC1);
	LL_ADC_INJ_StartConversion(ADC2);
	//Enable output onto gpio pins
	LL_HRTIM_EnableOutput(HRTIM1, LL_HRTIM_OUTPUT_TE1 | LL_HRTIM_OUTPUT_TE2 | LL_HRTIM_OUTPUT_TA1 | LL_HRTIM_OUTPUT_TA2);
	//Init ADC Filters
	Moving_Average_Init(&VinFilter, 40);
	Moving_Average_Init(&VoutFilter, 40);
	Moving_Average_Init(&CurInFilter, 40);
	Moving_Average_Init(&CurOutFilter, 40);
	//Enable Repetition Interrupt HRTIM
	LL_HRTIM_EnableIT_REP(HRTIM1, LL_HRTIM_TIMER_E);
	//Enable End of Injected Conversion Interrupt ADC
	LL_ADC_EnableIT_JEOS(ADC1);
	LL_ADC_EnableIT_JEOS(ADC2);
	//Enable 32Bit Timer for timing us events
	HAL_TIM_Base_Start(&htim5);
	__HAL_TIM_SET_PRESCALER(&htim5, HAL_RCC_GetPCLK1Freq() / 1000000 - 1);
	HAL_TIM_GenerateEvent(&htim5, TIM_EVENTSOURCE_UPDATE);

	__enable_irq();

	//Start HRTIM Counter
	LL_HRTIM_TIM_CounterEnable(HRTIM1, LL_HRTIM_TIMER_E | LL_HRTIM_TIMER_A);
	/* USER CODE END 2 */

	/* Infinite loop */
	/* USER CODE BEGIN WHILE */
	uint32_t nextSampleTime = 0;

	if (bq76_init(&battery_monitor, 0x01, 60, MAX_VCELL, 100, MIN_VCELL, 100, 60, 60, 100) != BQ76_OK)
	{
		bms_present = 0;
	}
	else
	{
		bms_present = 1;
	}

	while (1)
	{

		//Queue
		if (__HAL_TIM_GET_COUNTER(&htim5) >= nextSampleTime)
		{
			hostInterfaceQueueDeviceCMDExpl(OPSTATUS_OK, OPCODE_REPORT_LIVE_VALUE, OPTYPE_OUTPUT_VOLTAGE, VoutAverage);
			hostInterfaceQueueDeviceCMDExpl(OPSTATUS_OK, OPCODE_REPORT_LIVE_VALUE, OPTYPE_INPUT_VOLTAGE, VinAverage);
			hostInterfaceQueueDeviceCMDExpl(OPSTATUS_OK, OPCODE_REPORT_LIVE_VALUE, OPTYPE_OUTPUT_CURRENT, CurOutAverage);
			hostInterfaceQueueDeviceCMDExpl(OPSTATUS_OK, OPCODE_REPORT_LIVE_VALUE, OPTYPE_INPUT_CURRENT, CurInAverage);
			hostInterfaceQueueDeviceCMDExpl(OPSTATUS_OK, OPCODE_FINISHED_SAMPLE, OPTYPE_SAMPLE_NUM_OF_CHANNELS, 4);

			if (bms_present)
			{
				//Request Cell Voltage Conversion
				bq76_swrqst_adc_convert(&battery_monitor);

				//Read out cell voltages
				if (bq76_read_v_cells(&battery_monitor) != BQ76_OK)
				{
					bms_present = 0;
				}

				hostInterfaceQueueDeviceCMDExpl(OPSTATUS_OK, OPCODE_REPORT_CELL_VOLTAGE, 0, (int)battery_monitor.v_cells[0]);
				hostInterfaceQueueDeviceCMDExpl(OPSTATUS_OK, OPCODE_REPORT_CELL_VOLTAGE, 1, (int)battery_monitor.v_cells[1]);
				hostInterfaceQueueDeviceCMDExpl(OPSTATUS_OK, OPCODE_REPORT_CELL_VOLTAGE, 2, (int)battery_monitor.v_cells[2]);
				hostInterfaceQueueDeviceCMDExpl(OPSTATUS_OK, OPCODE_REPORT_CELL_VOLTAGE, 3, (int)battery_monitor.v_cells[3]);
				hostInterfaceQueueDeviceCMDExpl(OPSTATUS_OK, OPCODE_REPORT_CELL_VOLTAGE, 4, (int)battery_monitor.v_cells[4]);
				hostInterfaceQueueDeviceCMDExpl(OPSTATUS_OK, OPCODE_REPORT_CELL_VOLTAGE, 5, (int)battery_monitor.v_cells[5]);

				//Read status of device
				//bq76_read_alert_reg(&battery_monitor);
				//bq76_read_cov_fault_reg(&battery_monitor);
				//bq76_read_cuv_fault_reg(&battery_monitor);
				//bq76_read_fault_reg(&battery_monitor);
			}

			nextSampleTime = __HAL_TIM_GET_COUNTER(&htim5) + targetSampleDelay;
		}

		//Handle Host Interface
		hostInterfaceProcessCommand();

		/* USER CODE END WHILE */

		/* USER CODE BEGIN 3 */
	}
	/* USER CODE END 3 */
}

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
/* USER CODE BEGIN 4 */
int _write(int32_t file, uint8_t *ptr, int32_t len)
{
	/* Implement your write code here, this is used by puts and printf for example */
	int i = 0;
	for (i = 0; i < len; i++)
	{
		ITM_SendChar((*ptr++));
	}
	return len;
}

void HAL_SPI_RxCpltCallback(SPI_HandleTypeDef *hspi)
{
	if (battery_monitor.current_dma_request == BQ76_V_CELLS)
	{
		new_v_cell_data = 1;
	}
	handle_bq76_dma_callback(&battery_monitor);
}

/**
 * @brief  FLASH end of operation interrupt callback.
 * @param  ReturnValue: The value saved in this parameter depends on the ongoing procedure
 *                  Mass Erase: Bank number which has been requested to erase
 *                  Page Erase: Page which has been erased
 *                    (if 0xFFFFFFFF, it means that all the selected pages have been erased)
 *                  Program: Address which was selected for data program
 * @retval None
 */
void HAL_FLASH_EndOfOperationCallback(uint32_t ReturnValue)
{
	/* Call CleanUp callback when all requested pages have been erased */
	if (ReturnValue == 0xFFFFFFFF)
	{
		EE_EndOfCleanup_UserCallback();
	}
}

/**
 * @brief  Clean Up end of operation interrupt callback.
 * @param  None
 * @retval None
 */
void EE_EndOfCleanup_UserCallback(void)
{
	ErasingOnGoing = 0;
}

void writeEEPROM8(uint32_t Index, uint8_t data)
{
	/* Wait any cleanup is completed before accessing flash again */
	while (ErasingOnGoing == 1)
	{
	}

	EE_Status ee_status = EE_WriteVariable8bits(Index, data);

	/* Start cleanup IT mode, if cleanup is needed */
	if ((ee_status & EE_STATUSMASK_CLEANUP ) == EE_STATUSMASK_CLEANUP)
	{
		ErasingOnGoing = 1;
		ee_status |= EE_CleanUp_IT();
	}
	if ((ee_status & EE_STATUSMASK_ERROR ) == EE_STATUSMASK_ERROR)
	{
		Error_Handler();
	}
}

void writeEEPROM16(uint32_t Index, uint16_t data)
{
	/* Wait any cleanup is completed before accessing flash again */
	while (ErasingOnGoing == 1)
	{
	}

	EE_Status ee_status = EE_WriteVariable16bits(Index, data);

	/* Start cleanup IT mode, if cleanup is needed */
	if ((ee_status & EE_STATUSMASK_CLEANUP ) == EE_STATUSMASK_CLEANUP)
	{
		ErasingOnGoing = 1;
		ee_status |= EE_CleanUp_IT();
	}
	if ((ee_status & EE_STATUSMASK_ERROR ) == EE_STATUSMASK_ERROR)
	{
		Error_Handler();
	}
}

void writeEEPROM32(uint32_t Index, uint32_t data)
{
	/* Wait any cleanup is completed before accessing flash again */
	while (ErasingOnGoing == 1)
	{
	}

	EE_Status ee_status = EE_WriteVariable32bits(Index, data);

	/* Start cleanup IT mode, if cleanup is needed */
	if ((ee_status & EE_STATUSMASK_CLEANUP ) == EE_STATUSMASK_CLEANUP)
	{
		ErasingOnGoing = 1;
		ee_status |= EE_CleanUp_IT();
	}
	if ((ee_status & EE_STATUSMASK_ERROR ) == EE_STATUSMASK_ERROR)
	{
		Error_Handler();
	}
}

uint8_t readEEPROM8(uint32_t Index)
{
	/* Wait any cleanup is completed before accessing flash again */
	while (ErasingOnGoing == 1)
	{
	}

	uint8_t dataOut = 0;

	EE_Status ee_status = EE_ReadVariable8bits(Index, &dataOut);

	/* Start cleanup IT mode, if cleanup is needed */
	if ((ee_status & EE_STATUSMASK_CLEANUP ) == EE_STATUSMASK_CLEANUP)
	{
		ErasingOnGoing = 1;
		ee_status |= EE_CleanUp_IT();
	}
	if ((ee_status & EE_STATUSMASK_ERROR ) == EE_STATUSMASK_ERROR)
	{
		Error_Handler();
	}
	return dataOut;
}

uint16_t readEEPROM16(uint32_t Index)
{
	/* Wait any cleanup is completed before accessing flash again */
	while (ErasingOnGoing == 1)
	{
	}

	uint16_t dataOut = 0;

	EE_Status ee_status = EE_ReadVariable16bits(Index, &dataOut);

	/* Start cleanup IT mode, if cleanup is needed */
	if ((ee_status & EE_STATUSMASK_CLEANUP ) == EE_STATUSMASK_CLEANUP)
	{
		ErasingOnGoing = 1;
		ee_status |= EE_CleanUp_IT();
	}
	if ((ee_status & EE_STATUSMASK_ERROR ) == EE_STATUSMASK_ERROR)
	{
		Error_Handler();
	}
	return dataOut;
}

uint32_t readEEPROM32(uint32_t Index)
{
	/* Wait any cleanup is completed before accessing flash again */
	while (ErasingOnGoing == 1)
	{
	}

	uint32_t dataOut = 0;

	EE_Status ee_status = EE_ReadVariable32bits(Index, &dataOut);

	/* Start cleanup IT mode, if cleanup is needed */
	if ((ee_status & EE_STATUSMASK_CLEANUP ) == EE_STATUSMASK_CLEANUP)
	{
		ErasingOnGoing = 1;
		ee_status |= EE_CleanUp_IT();
	}
	if ((ee_status & EE_STATUSMASK_ERROR ) == EE_STATUSMASK_ERROR)
	{
		Error_Handler();
	}
	return dataOut;
}
/* USER CODE END 4 */
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


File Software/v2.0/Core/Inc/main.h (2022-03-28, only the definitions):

#define CHGPMP_PERIOD 8500
#define PWM_PERIOD 36267
#define DEAD_TIME 80
#define DBG_LED4_Pin GPIO_PIN_13
#define DBG_LED4_GPIO_Port GPIOC
#define DBG_LED3_Pin GPIO_PIN_14
#define DBG_LED3_GPIO_Port GPIOC
#define DBG_LED2_Pin GPIO_PIN_15
#define DBG_LED2_GPIO_Port GPIOC
#define DBG_LED1_Pin GPIO_PIN_2
#define DBG_LED1_GPIO_Port GPIOC
#define VIN_CHGPMP_Pin GPIO_PIN_3
#define VIN_CHGPMP_GPIO_Port GPIOC
#define VOUT_CHGPMP_Pin GPIO_PIN_2
#define VOUT_CHGPMP_GPIO_Port GPIOB
#define BQ_NSS_Pin GPIO_PIN_12
#define BQ_NSS_GPIO_Port GPIOB
#define MAX_VCELL   4.2f
#define MIN_VCELL   2.5f
#define UPPER_DC_LIMIT_BUCK	PWM_PERIOD * 0.95
#define LOWER_DC_LIMIT_BUCK	PWM_PERIOD * 0.05
#define UPPER_DC_LIMIT_BOOST	PWM_PERIOD * 0.95
#define LOWER_DC_LIMIT_BOOST	PWM_PERIOD * 0.05
#define UPPER_DC_LIMIT_BUCKBOOST	PWM_PERIOD * 0.95
#define LOWER_DC_LIMIT_BUCKBOOST	PWM_PERIOD * 0.05
#define CONVERSION_STATE_SHUTDOWN	0
#define CONVERSION_STATE_BUCK		1
#define CONVERSION_STATE_BOOST		2
#define CONVERSION_STATE_BUCKBOOST	3
#define CONVERSION_STATE_PWM_OFFSET 10000
#define OVER_VOLTAGE_PROTECTION			30000
#define UNDER_VOLTAGE_PROTECTION		5000
#define OVER_CURRENT_PROTECTION			10000
#define REVERSE_CURRENT_PROTECTION	-100
#define BUCK_BOOST_BAND 								3000
#define BUCK_BOOST_BAND_HYSTERESIS 			800
#define VDDA						3300
#define ADC_OVERSAMPLING_X2		0x1FFE
#define ADC_OVERSAMPLING_X4		0x3FFC
#define ADC_OVERSAMPLING_X8		0x7FF8
#define ADC_OVERSAMPLING_X16	0xFFF0
#define VIN_VDIV_RUP	820
#define VIN_VDIV_RLOW	43
#define CURIN_AMP_FACTOR 		50		//INA240A2 Amplification
#define CURIN_SHUNT_FAC			200		//1 / ShuntResistance = 1 / 5mR = 200
#define CURIN_VOLTAGE_REF 	340		//340mV Shunt Amplifier Offset
#define VOUT_VDIV_RUP		820
#define VOUT_VDIV_RLOW	43
#define CUROUT_AMP_FACTOR 	50		//INA240A2 Amplification
#define CUROUT_SHUNT_FAC		200		//1 / ShuntResistance = 1 / 5mR = 200
#define CUROUT_VOLTAGE_REF 	340		//340mV Shunt Amplifier Offset

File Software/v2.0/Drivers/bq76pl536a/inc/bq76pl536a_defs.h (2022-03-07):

/******************************************************************************
 *
 * @file	bq76pl536a_defs.h
 * @brief 	Texas Instruments BQ76PL536A register and constants definitions
 * @version	v1.00f00
 * @date	27, Dec. 2020
 * @author	CECARELLI, Federico (fededc88@gmail.com),
 * 			MOYA, Martin		(moyamartin1@gmail.com),
 * 			SANTOS, Lucio		(lusho2206@gmail.com)
 * @copyright GPL license, all text here must be included in any redistribution
 *****************************************************************************/

#ifndef __BQ76PL536A_DEFS_H_
#define __BQ76PL536A_DEFS_H_

#include <stdint.h>

/** 
 * BQ76PL536A Status Register address 
 *	Default value: 0b00000000 0x00
 *	Type: R - GROUP 1
 */
#define DEVICE_STATUS_REG		(0x00)

/** 
 * BQ76PL536A GPAI Low Data Register address 
 *	Default value: 0b00000000 0x00
 *	Type: R - GROUP 1
 */
#define GPAI_LOW_REG			(0x01)

/** 
 * BQ76PL536A GPAI High Data Register address 
 *	Default value: 0b00000000 0x00
 *	Type: R - GROUP 1
 */
#define GPAI_HIGH_REG			(0x02)

/** 
 * BQ76PL536A VCELL1 Low Data Register address 
 *	Default value: 0b00000000 0x00
 *	Type: R - GROUP 1
 */
#define VCELL1_LOW_REG			(0x03)

/** 
 * BQ76PL536A VCELL1 High Data Register address 
 *	Default value: 0b00000000 0x00
 *	Type: R - GROUP 1
 */
#define VCELL1_HIGH_REG			(0x04)

/** 
 * BQ76PL536A VCELL2 Low Data Register address 
 *	Default value: 0b00000000 0x00
 *	Type: R - GROUP 1
 */
#define VCELL2_LOW_REG			(0x05)

/** 
 * BQ76PL536A VCELL2 High Data Register address 
 *	Default value: 0b00000000 0x00
 *	Type: R - GROUP 1
 */
#define VCELL2_HIGH_REG			(0x06)

/** 
 * BQ76PL536A VCELL3 Low Data Register address 
 *	Default value: 0b00000000 0x00
 *	Type: R - GROUP 1
 */
#define VCELL3_LOW_REG			(0x07)

/** 
 * BQ76PL536A VCELL3 High Data Register address 
 *	Default value: 0b00000000 0x00
 *	Type: R - GROUP 1
 */
#define VCELL3_HIGH_REG			(0x08)

/** 
 * BQ76PL536A VCELL4 Low Data Register address 
 *	Default value: 0b00000000 0x00
 *	Type: R - GROUP 1
 */
#define VCELL4_LOW_REG			(0x09)

/** 
 * BQ76PL536A VCELL4 High Data Register address 
 *	Default value: 0b00000000 0x00
 *	Type: R - GROUP 1
 */
#define VCELL4_HIGH_REG			(0x0a)

/** 
 * BQ76PL536A VCELL5 Low Data Register address 
 *	Default value: 0b00000000 0x00
 *	Type: R - GROUP 1
 */
#define VCELL5_LOW_REG			(0x0b)

/** 
 * BQ76PL536A VCELL5 High Data Register address 
 *	Default value: 0b00000000 0x00
 *	Type: R - GROUP 1
 */
#define VCELL5_HIGH_REG			(0x0c)

/** 
 * BQ76PL536A VCELL6 Low Data Register address 
 *	Default value: 0b00000000 0x00 
 *	Type: R - GROUP 1
 */
#define VCELL6_LOW_REG			(0x0d)

/** 
 * BQ76PL536A VCELL6 High Data Register address 
 *	Default value: 0b00000000 0x00
 *	Type: R - GROUP 1
 */
#define VCELL6_HIGH_REG			(0x0e)

/** 
 * BQ76PL536A TEMPERATURE1 Low Data Register address 
 *	Default value: 0b00000000 0x00
 *	Type: R - GROUP 1
 */
#define TEMPERATURE1_LOW_REG 	(0x0f)

/** 
 * BQ76PL536A TEMPERATURE1 High Data Register address 
 *	Default value: 0b00000000 0x00
 *	Type: R - GROUP 1
 */
#define TEMPERATURE1_HIGH_REG	(0x10)

/** 
 * BQ76PL536A TEMPERATURE2 Low Data Register address 
 *	Default value: 0b00000000 0x00
 *	Type: R - GROUP 1
 */
#define TEMPERATURE2_LOW_REG 	(0x11)

/** 
 * BQ76PL536A TEMPERATURE2 High Data Register address 
 :	Default value: 0b00000000 0x00
 *	Type: R - GROUP 1
 */
#define TEMPERATURE2_HIGH_REG	(0x12)

/** 
 * BQ76PL536A Alert Status Register address 
 *	Default value: 0b10000000 0x80
 *	Type: R/W - GROUP 2
 */
#define ALERT_STATUS_REG		(0x20)

/** 
 * BQ76PL536A Fault Status Register address 
 *	Default value: 0b00001000 0x08
 *	Type: R/W - GROUP 2
 */
#define FAULT_STATUS_REG		(0x21)

/** 
 * BQ76PL536A COV Fault Status Register address 
 *	Default value: 0b00000000 0x00
 *	Type: R - GROUP 1
 */
#define COV_FAULT_REG			(0x22) 

/** 
 * BQ76PL536A CUV Fault Status Register address 
 *	Default value: 0b00000000 0x00
 *	Type: R - GROUP 1
 */
#define CUV_FAULT_REG			(0x23)

/** 
 * BQ76PL536A Preresult A Status Register address 
 *	Default value: 0b00000000 0x00
 *	Type: R - GROUP 1
 */
#define PRESULT_A_REG			(0x24)

/** 
 * BQ76PL536A Preresult B Status Register address 
 *	Default value: 0b00000000 0x00
 *	Type: R - GROUP 1
 */
#define PRESULT_B_REG			(0x25)

/** 
 * BQ76PL536A ADC Control Register address 
 *	Default value: 0b00000000 0x00
 *	Type: R/W - GROUP 2
 */
#define ADC_CONTROL_REG			(0x30)

/** 
 * BQ76PL536A IO Control Register address 
 *	Default value: 0b00000000 0x00
 *	Type: R/W - GROUP 2
 */
#define IO_CONTROL_REG			(0x31)

/** 
 * BQ76PL536A CB Control Register address 
 *	Default value: 0b00000000 0x00
 *	Type: R/W - GROUP 2
 */
#define CB_CONTROL_REG			(0x32)

/** 
 * BQ76PL536A CB Time Register address 
 *	Default value: 0b00000000 0x00
 *	Type: R/W - GROUP 2
 */
#define CB_TIME_REG				(0x33)

/** 
 * BQ76PL536A ADC Convert address 
 *	Default value: 0b00000000 0x00
 *	Type: R/W - GROUP 2
 */
#define ADC_CONVERT_REG			(0x34)
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

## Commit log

2020-09-13 Initialized Altium Project
    [SCC.PcbDoc, SCC.PrjPcb, SCC.SchDoc]
2020-09-16 Added DesignGuide
    [SCC.SchDoc]
2020-09-30 Added BOBs, added CubeMX project
    [BSC0802BOB.PcbDoc, BSC0802BOB.SchDoc, DevBOB.PcbDoc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]
2020-10-06 Added Design guide, removed cubeMx project
    [DevBOB.PcbDoc, DevBOB.SchDoc, DevBOBPanel.PcbDoc]
2020-10-20 restarted Altium project, added buck converter
    [BSC0802BOB.PcbDoc, BSC0802BOB.SchDoc, DevBOB.PrjPcb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]
2020-10-22 refactored Altium projects
    [RcMPPT-BMS.PcbDoc, RcMPPT-BMS.PrjPcb, RcMPPT-BMS.SchDoc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]
2020-10-28 added MCU and peripherals
    [RcMPPT-DCDC.SchDoc, RcMPPT-MCU.SchDoc, RcMPPT-Power_Module.SchDoc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]
2020-10-29 added additional MCU peripherals
    [RcMPPT-DCDC.SchDoc, RcMPPT-MCU.SchDoc, RcMPPT-SCC.PcbDoc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]
2020-10-31 added Multiboard-Assembly
    [RcMPPT-BMS.PcbDoc, RcMPPT-DCDC.SchDoc, RcMPPT-MCU.SchDoc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]
2020-11-02 routed majority of MCU peripherals
    [RcMPPT-BMS.PcbDoc, RcMPPT-BMS.SchDoc, RcMPPT-MCU.SchDoc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]
2020-11-06 Schematic develoment
2020-11-06 Revert "Schematic develoment"
    This reverts commit 58956fab0cb714e4bc268e1affdffaedeebbf3e4.
2020-11-07 added SmartPdf
    [RcMPPT-DCDC.SchDoc, RcMPPT-MCU.SchDoc, RcMPPT-SCC.PcbDoc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]
2020-12-30 added design guides, added dcdc-schematic
    [RcMPPT-DCDC.SchDoc, RcMPPT-MCU.SchDoc, RcMPPT-Power_Module.SchDoc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]
2020-12-31 Revert "Merge branch 'master' of https://github.com/ThoMint/RcMPPT"
    This reverts commit 729b1848ecf8b00d021b4e46789bf0435b2d80fc, reversing
    changes made to 842d05084a4867483b0c6199020a9ef9159179db.
    [RcMPPT-DCDC.SchDoc, RcMPPT-MCU.SchDoc, RcMPPT-Power_Module.SchDoc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]
2021-01-09 pcb advancements
    redesigned pcb
    [RcMPPT-DCDC.SchDoc, RcMPPT-MCU.SchDoc, RcMPPT-Power_Module.SchDoc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]
2021-01-22 advanced in IO capabilitys and analog circutry
    [BomTemplate.xls, RcMPPT-BMS.SchDoc, RcMPPT-DCDC.SchDoc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]
2021-01-27 finished version 1.0
    [RcMPPT-DCDC.SchDoc, RcMPPT-IO.SchDoc, RcMPPT-Power_Module.SchDoc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]
2021-01-29 refined pcb stackup and impedance profiles
    [RcMPPT-DCDC.SchDoc, RcMPPT-MCU.SchDoc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]
2021-02-01 advanced pcb, refactored software project
    [RcMPPT-DCDC.SchDoc, RcMPPT-IO.SchDoc, RcMPPT-MCU.SchDoc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]
2021-02-04 added IO and analog filtering
    [RcMPPT-DCDC.SchDoc, RcMPPT-IO.SchDoc, RcMPPT-MCU.SchDoc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]
2021-02-04 added Silkscreen, sectioned Schematics
    [RcMPPT-DCDC.SchDoc, RcMPPT-IO.SchDoc, RcMPPT-MCU.SchDoc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]
2021-02-04 fixed SPI missing CS
    [RcMPPT-BMS.PcbDoc, RcMPPT-IO.SchDoc, RcMPPT-MCU.SchDoc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]
2021-02-09 finalized v1, added gerber files
    [RcMPPT-DCDC.SchDoc, RcMPPT-MCU.SchDoc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]
2021-03-15 software dev
    [RcMPPT-DCDC.SchDoc, RcMPPT-SCC.xlsx]
2021-04-07 Hotfix
    several capacitors were causing the charge-pumps to overdrive the voltage at the boostrap capacitors
    [RcMPPT-DCDC.SchDoc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]
2021-06-03 updated firmware, added design guides
    [RcMPPT-DCDC.SchDoc, RcMPPT-SCC.PrjPcb]
2021-09-29 changed project structure
    [LMZ36002RVQT.PcbLib, LMZ36002RVQT.SchLib, RcMPPT-BMS.PcbDoc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]
2021-11-04 added errata, started schematik dev v2.0, added custom window size on average
    [RcMPPT-DCDC.SchDoc, RcMPPT-IO.SchDoc, RcMPPT-MCU.SchDoc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]
2021-11-10 started converting schematics to hierarchical
    [RcMPPT-DCDC.SchDoc, RcMPPT-Debug.SchDoc, RcMPPT-IO.SchDoc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]
2021-11-24 changed bom strategy and moved to hierarchical schematics design
    [RcMPPT-BMS.PcbDoc, RcMPPT-BMS.PrjPcb, RcMPPT-BMS.SchDoc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]
2021-12-12 schematic development
    changed design guide folder structure; added bms schematics; polished hierarchical layout
    [RcMPPT-BMS-AFE1.SchDoc, RcMPPT-BMS-AFE2.SchDoc, RcMPPT-BMS-BFE.SchDoc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]
2021-12-23 schematic development, first pcb layout prototype
    [RcMPPT-BMS-AFE1.SchDoc, RcMPPT-BMS-AFE2.SchDoc, RcMPPT-BMS-BFE.SchDoc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]
2022-01-03 bms and scc pcb design
    [RcMPPT-BMS-AFE1.SchDoc, RcMPPT-BMS-AFE2.SchDoc, RcMPPT-BMS-BFE.SchDoc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]
2022-01-12 pcb development
    [20021521-00010XXLFc.stp, DF13A-6P-1.25H.stp, RcMPPT-BMS-AFE1.SchDoc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]
2022-01-16 finished pcb design and mba
    [128x32-OLED.STEP, DF13A-4P-1.25H.stp, RcMPPT-BMS-Interface.SchDoc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]
2022-01-19 refined hardware design
    [RcMPPT-BMS.PcbDoc, RcMPPT-Debug.SchDoc, RcMPPT-IO.SchDoc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]
2022-01-20 generated gerber files for production
    [RcMPPT-BMS.GBL, RcMPPT-BMS.GBO, RcMPPT-BMS.GBS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]
2022-03-07 ported software to version 2.0 hardware, fixed hardware bug on bms interface
    [RcMPPT-BMS-AFE1.SchDoc, RcMPPT-BMS-AFE2.SchDoc, RcMPPT-BMS-BFE.SchDoc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]
2022-03-09 fine tuned schematics for documentation
    [RcMPPT-BMS.PrjPcb, RcMPPT-IO.SchDoc, RcMPPT-SCC (1).xls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]
2022-03-17 updated hardware documentation
    [RcMPPT-BMS-AFE1.SchDoc, RcMPPT-BMS-AFE2.SchDoc, RcMPPT-BMS-BFE.SchDoc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]
2022-03-28 firmware dev and added mouser BOM export
    [RcMPPT-BMS (2).xlsx]
2022-03-31 updated hardware documentation - diploma thesis hand in
    [RcMPPT-BMS-AFE1.SchDoc, RcMPPT-BMS-AFE2.SchDoc, RcMPPT-BMS-Interface.SchDoc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]

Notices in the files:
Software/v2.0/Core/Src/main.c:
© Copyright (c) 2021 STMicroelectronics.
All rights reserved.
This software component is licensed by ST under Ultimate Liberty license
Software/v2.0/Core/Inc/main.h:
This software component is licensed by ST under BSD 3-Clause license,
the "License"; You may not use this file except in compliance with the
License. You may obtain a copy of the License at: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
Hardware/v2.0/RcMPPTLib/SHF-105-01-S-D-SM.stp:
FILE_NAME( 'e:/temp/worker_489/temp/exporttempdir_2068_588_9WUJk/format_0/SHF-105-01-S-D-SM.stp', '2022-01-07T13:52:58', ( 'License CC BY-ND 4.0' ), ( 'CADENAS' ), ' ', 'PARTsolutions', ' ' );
